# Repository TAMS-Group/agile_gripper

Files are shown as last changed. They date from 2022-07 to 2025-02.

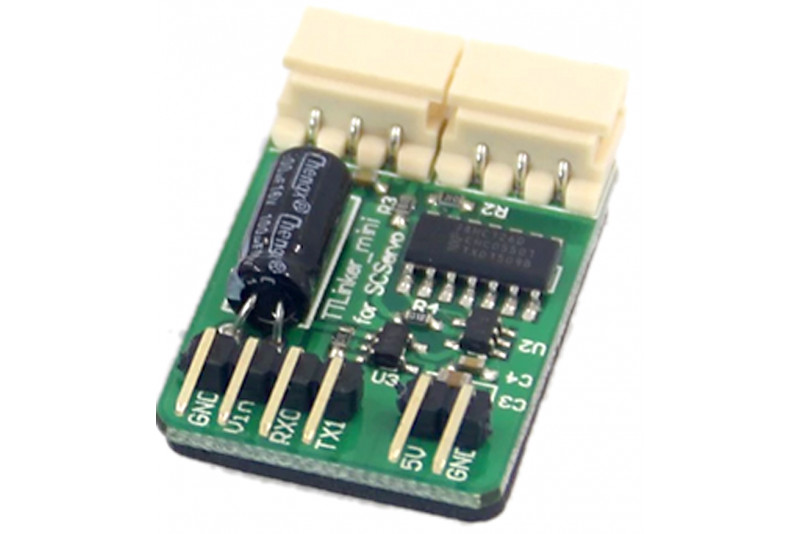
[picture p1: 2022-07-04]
doc/ttlinker-mini-pinout.jpg

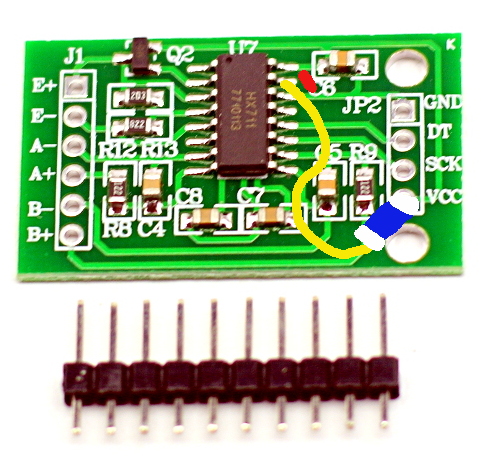
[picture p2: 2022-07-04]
doc/HX711_board_cut_instruction.jpg

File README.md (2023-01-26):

# diana_gripper: Versatile 2-finger 4-servo gripper driven by Feetech SCS digital bus servos

This ROS package provides robot-models and software for a versatile
two-finger gripper using four digital-bus servos from Feetech Inc.

* Using four rotational joints, the gripper can execute parallel
  pinch grasps and tip-pinch grasps, but the fingers can also wrap
  around an object (e.g. a bottle) if needed.

* The fingertips can be easily exchanged. We provide URDF models
  for generic fixed fingers, finray-style flexible fingers,
  and adapters for mounting the camera-based high-res tactile
  DIGIT sensors.

* Both fingers are mounted on a pair of standard load-cells,
  providing measurements of grasping force and shearing force.

* Our Arduino firmware also supports multiple optional 
  finger-mounted IMUs, which can be used to measure vibration,
  impact, and fingertip orientation.

* The SCS-20 servo already provides a lot of sensor inputs,
  including joint (finger) position, velocity, motor torque,
  motor voltage and current, and motor temperature.

## Hardware Overview

## Electronics Overview 

The suggested electronics is based on an Arduino Nano 33 IOT
microcontroller, which includes another IMU (STM LSM6DS3).
The first serial interface (pins RX/TX) of the Nano 33 IOT
is connected to a Feetech "TTLinker Mini" board,
which in turn controls the SCS-20 servos.

Both GY-521 boards are connected to the first I2C-bus (pins A4/A5)
and are powered from the 5V/VUSB pin of the Arduino,
which requires to bridge the corresponding jumper on the
underside of the Nano 33 IOT. 
The GY-521 includes its own 5V->3V3 regulator and data 
communication uses 3V3 levels, compatible with the Nano 33 IOT.
Allocated I2C addresses are 0x68 and 0x69 for the GY-521 boards,
and 0x6A for the on-board LSM6DS3.

The load-cells of both fingers are connected to a common
HX-711 chip breakout board each. The HX-711 provides all
required amplification and filtering circuits together with
a 24-bit ADC running at roughly 80 Hz sample rate.
The digital interface only requires two lines (CLK, Data) each,
connected to the Arduino pins (D2,D3), (D4,D5), (D6,D7), and (D8,D9).

Communication with the host is via USB, and the whole electronics
is bus-powered by the USB. 
Of course, the SCS-20 servos require its own power supply (e.g. 7.2V, 8A).
For now, the 3V3 supply from the Arduino is used to power the load-cells,
as the HX-711 is specified for 2.7..5.5V. Using a stabilitzed
5V supply might increase signal-to-noise ratio. but the 5V USB
is too noisy for that, and another power supply would add to the
hardware complexity.

## udev device detection

The arduino transmits a (unique?) id that can be matched in
udev to identify the serial device. doc/10-diana-gripper-udev.rules
provides a rule file that can be copied to /etc/udev/rules.d/ to add a symlink
/dev/diana_gripper pointing to the correct device.

## Arduino Nano 33 IOT I2C Problems

Maybe try an active bus transceiver or at least a bus terminator, e.g.
https://learn.adafruit.com/adafruit-ltc4311-i2c-extender-active-terminator

See ~/.arduino15/packages/arduino/hardware/samd/1.8.11/cores/arduino/wiring_private.c
and below for the pin assignments and pin capabilities of your specific board.
Then try to edit the source for the Wire library a bit:
/homeL/hendrich/.arduino15/packages/arduino/hardware/samd/1.8.11/libraries/Wire

```
...
void TwoWire::begin(void) {
  //Master Mode
  sercom->initMasterWIRE(TWI_CLOCK);
  sercom->enableWIRE();

  pinPeripheral(_uc_pinSDA, g_APinDescription[_uc_pinSDA].ulPinType);
  pinPeripheral(_uc_pinSCL, g_APinDescription[_uc_pinSCL].ulPinType);
  // FNH! I2C always dying on Arduino Nano 33 IOT... see cores/arduino/wiring_private.c
   PORT->Group[g_APinDescription[_uc_pinSDA].ulPort].PINCFG[g_APinDescription[_uc_pinSDA].ulPin].reg |= (uint8_t) (PORT_PINCFG_DRVSTR);
   PORT->Group[g_APinDescription[_uc_pinSCL].ulPort].PINCFG[g_APinDescription[_uc_pinSCL].ulPin].reg |= (uint8_t) (PORT_PINCFG_DRVSTR);
   // FNH end 
}
...
```

## Servo-Commander firmware

The SCS commander utility scans the bus for devices and reports
all detected servos, together with their protocol type.
Once the initial scan is completed, the commander enters an
interactive loop where the user can select the active servo
and then execute read/write commands on the selected servo.

The SCS commander is not using ROS. 
The program is supposed to be used with a terminal application
or the serial console from the Arduino IDE.
All commands should be terminated by a \n character, either
\f (linefeed) or \r (carriage-return) or both.

* S <id>\n : select servo at address <id> (decimal 3..253) for 
  the next commands.

* i\n :    print motor current (SCS) (may read -1: not implemented by servo)
* j\n :    print motor current (SMS) as multiple of 0.01A 

* l\n :    print motor load (torque) (SCS), unknown units
* m\n :    print motor load (torque) (SMS), unknown units

* p\n :    print motor position (SCS), counts (0..1023)
* q\n :    print motor position (SMS), counts (0..4095)

* t\n :    print servo temperature  (degrees celsius)

* v\n :    print servo supply voltage (deci-volts)

* P <pos>\n:  (SCS-only) move to given position (counts) using current
           speed and/or duration

* Q <pos>\n:  (SMS-only) move to given position (counts) using
              current max-speed and max-acceleration

* S <speed>\n: set motion speed for next P/Q command

## Gripper / Hand firmware and command set

The hand microcontroller currently uses ASCII-based communication
with the host, so that debug messages appear as plain text in the
output stream, and motor values are also human-readable. 

The following lists summarize the most common output messages
and commands (input messages), but may be out-of-sync with the
current release. Please check the source code for the actually
implemented versions and their formatting.

### Firmware output ROS topics:

<node_name>/joint_states          (sensor_msgs/JointState)
<node_name>/joint_errors          (sensor_msgs/JointState: pos=pos vel=vel eff=pos-error)
<node_name>/voltages              (sensor_msgs/Joy: axes:raw values)
<node_name>/temperatures          (sensor_msgs/Joy: axes:raw values)
<node_name>/currents
<node_name>/forces_raw            (sensor_msgs/Joy: axes: raw values)
<node_name>/palm_imu_raw          (sensor_msgs/Imu)
<node_name>/left_finger_imu_raw   (sensor_msgs/Imu)
<node_name>/right_finger_imu_raw  (sensor_msgs/Imu)

### Firmware output messages from the hand

* E: servo position errors (current - goal)
 
  E seq_number stamp pos err1 err2 err3 err4

  published as joint_state message on topic ~joint_position_errors
  with <effort> = errors, <pos> = current servo positions, <vel> =
  current servo velocities

* F: "forces" current force measurementss in Ascii format

  F seq_number stamp forces lc1 lc2 lc3 lc4

  Latest raw values from the load-cells, as measured by
  the HX-711 A/D converters.
  No scaling or temperature compensation is
  applied to the values, which are published as joy messages
  on topic ~/forces_raw and zero-biased on ~/forces_cooked.

  Exponential filtering with alpha=0.1 and 0.01 is also 
  applied to the values to generate high-pass filtered versions
  on topics ~force_filtered_10 and  ~forces_filtered_100

* I: "current" servo motor currents (in Feetech units)

  I seq_number stamp amps i1 i2 i3 i4

  published as joy messages on topic ~currents

* M: "moments" servo motor torques (in Feetech units)

  M seq_number stamp trq m1 m2 m3 m4

  Stored in internal variable and sent as part of 
  next '''joint_state message'''. Also re-published as raw-values 
  (servo counts) to the '''~torques''' topic.

* P: "positions" servo positions (in Feetech counts)

  P seq_number stamp pos p1 p2 p3 p4

  Published as joint_state on topic ~joint_states, where
  <position> = incoming positions converted to radians,
  <velocity> = joint velocity in radians/sec calculated from current
               and previous position message (numerical difference),
               or zero unless at least two messages have been received,
  <effort>   = torques from pervious "M" message

* T: "temperatures" current servo temperaturs in degrees celsius

  T seq_number stamp temp t1 t2 t3 t4 t5 t6 t7

  published as joy messages on topic ~temperatures

* U: "voltages" current servo supply voltages (in deci-volts)

  U seq_number stamp volts u1 u2 u3 u4 u5 u6 u7

  published as joy messages on topic ~voltages

* V: "velocities" current servo velocities (in Feetech units)

  V seq_number stamp vel v1 v2 v3 v4 v5 v6 v7

  currently not used or re-published as ROS message

### Text-commands currently supported by the hand firmware:

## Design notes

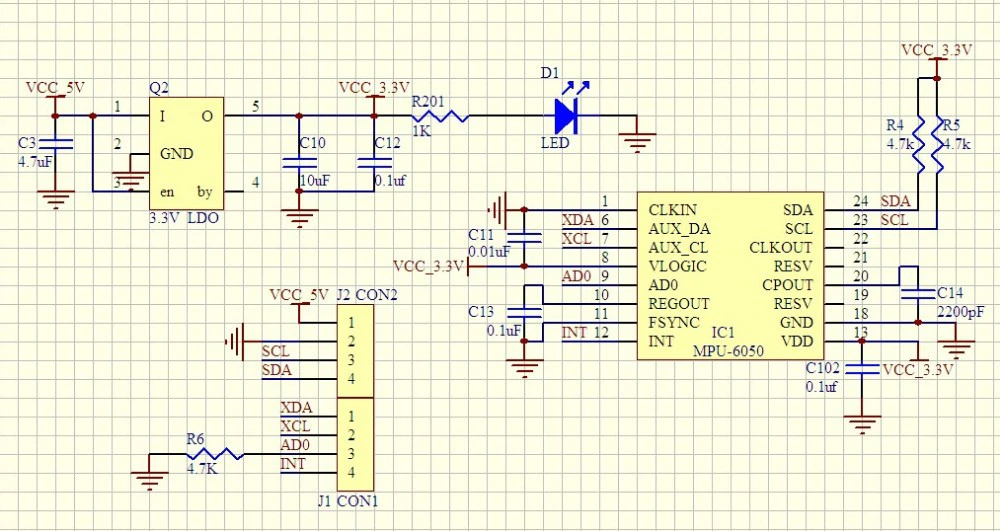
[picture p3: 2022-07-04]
doc/GY-521-schematics.png

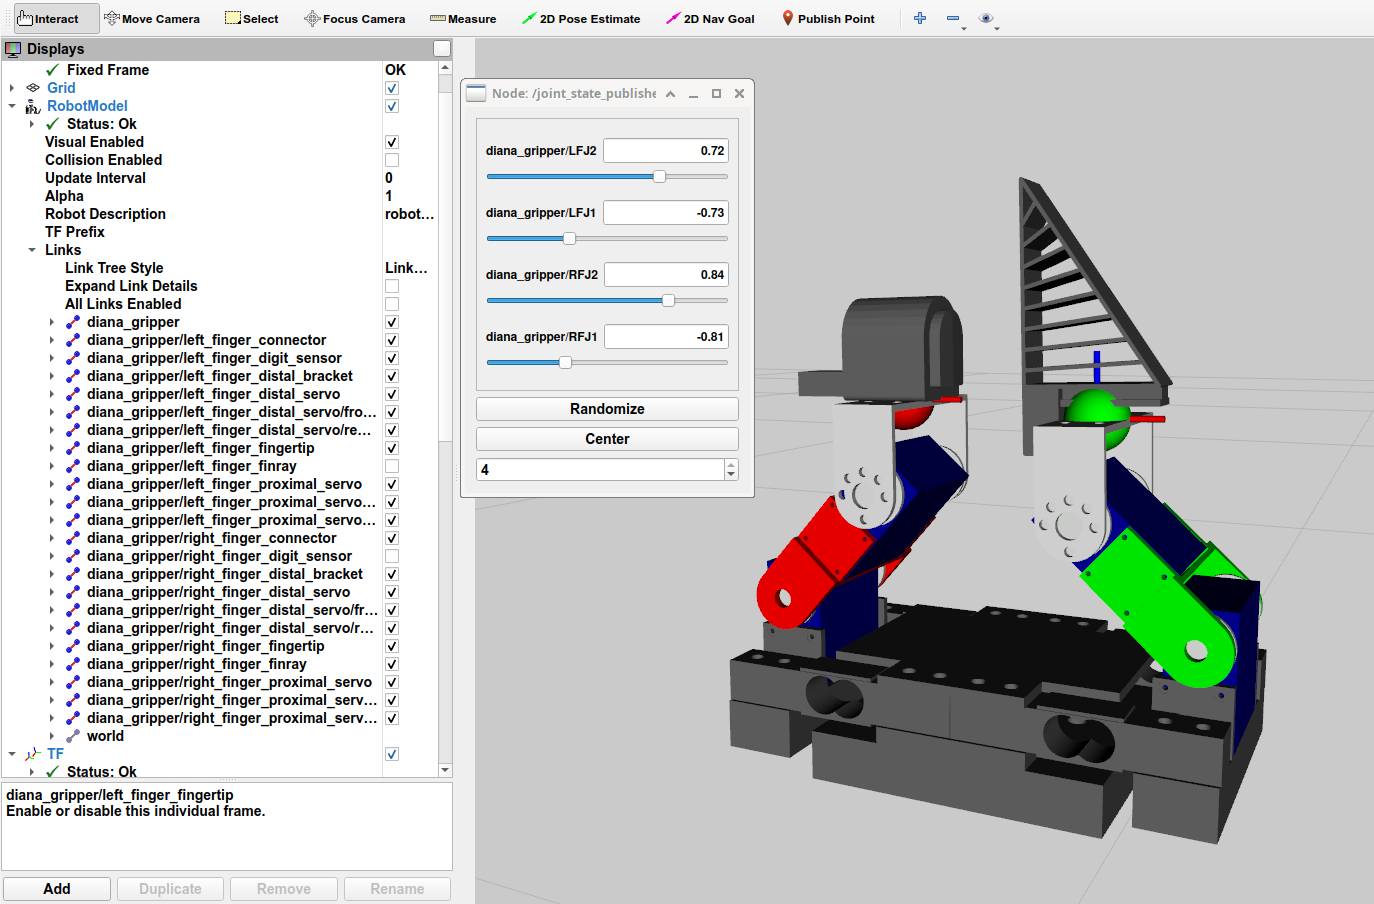
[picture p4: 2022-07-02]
doc/diana_gripper_digit_finray_rviz.png

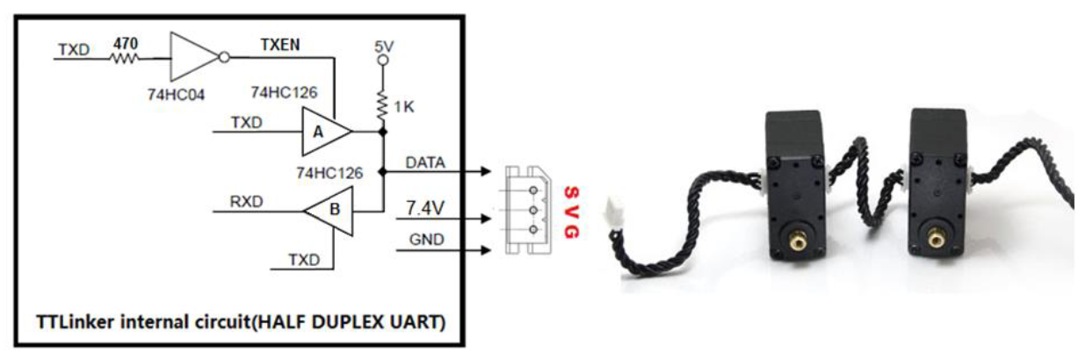
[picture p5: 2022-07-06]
doc/ttlinker-internal-circuit.png

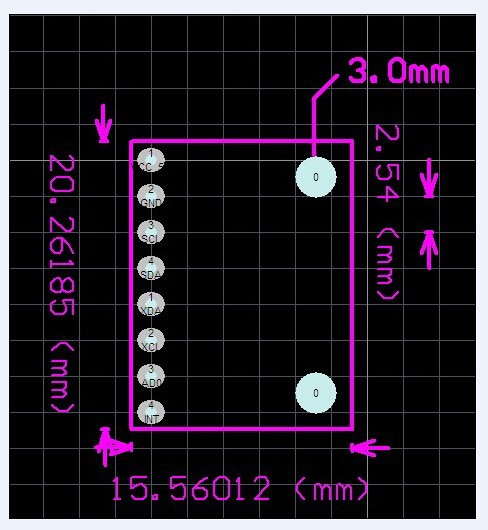
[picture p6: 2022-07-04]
doc/GY-521-dimensions.png

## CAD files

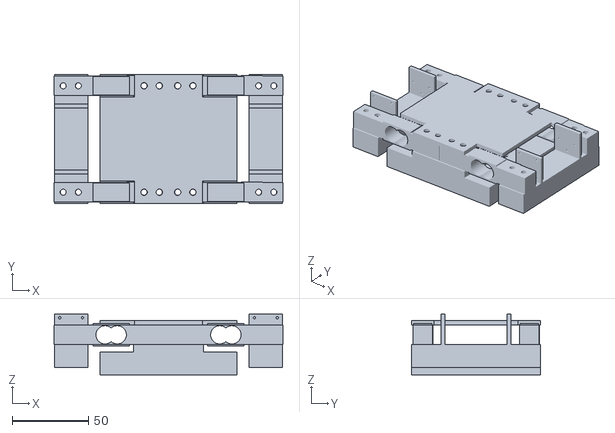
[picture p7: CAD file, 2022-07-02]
meshes/diana_gripper_base_complete_v1.stl
150.6 x 85.0 x 40.0

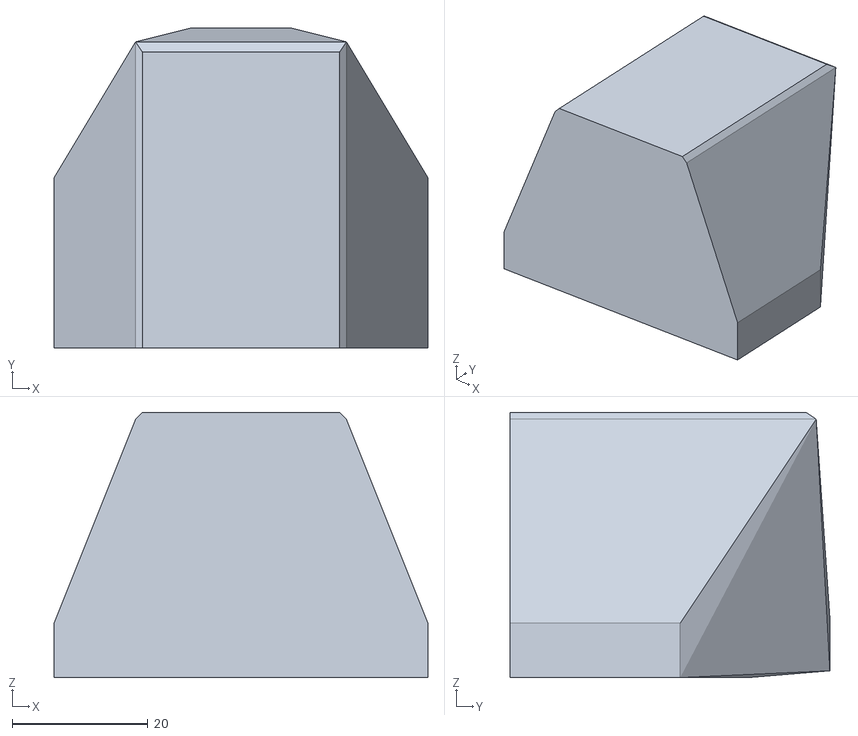
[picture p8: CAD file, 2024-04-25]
meshes/multitip_hull.stl
55.0 x 47.0 x 39.0

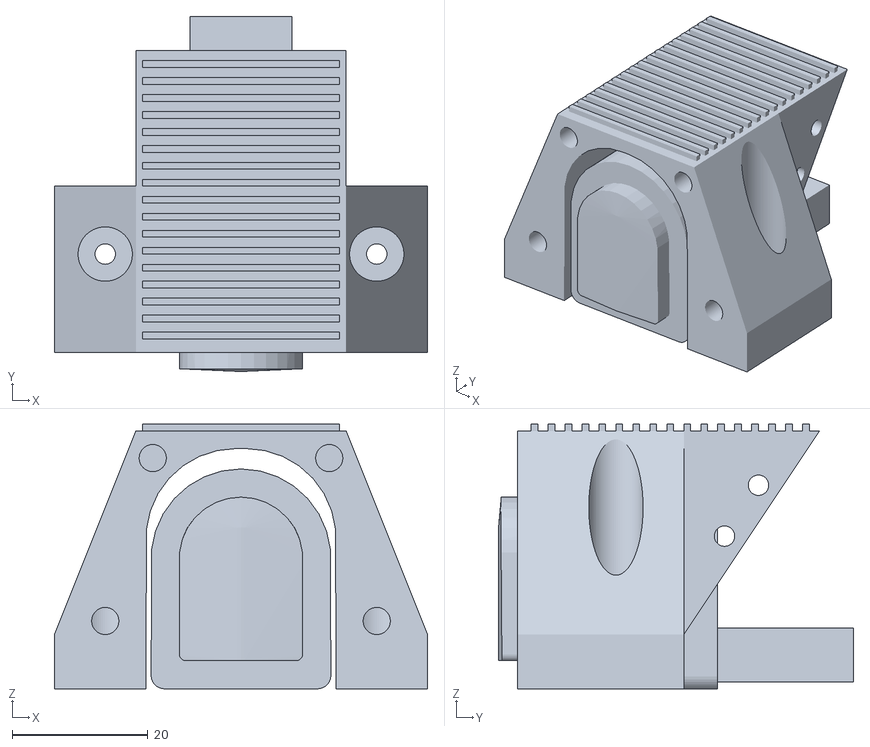
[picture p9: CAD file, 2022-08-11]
meshes/multitip.stl
55.0 x 52.3 x 39.0

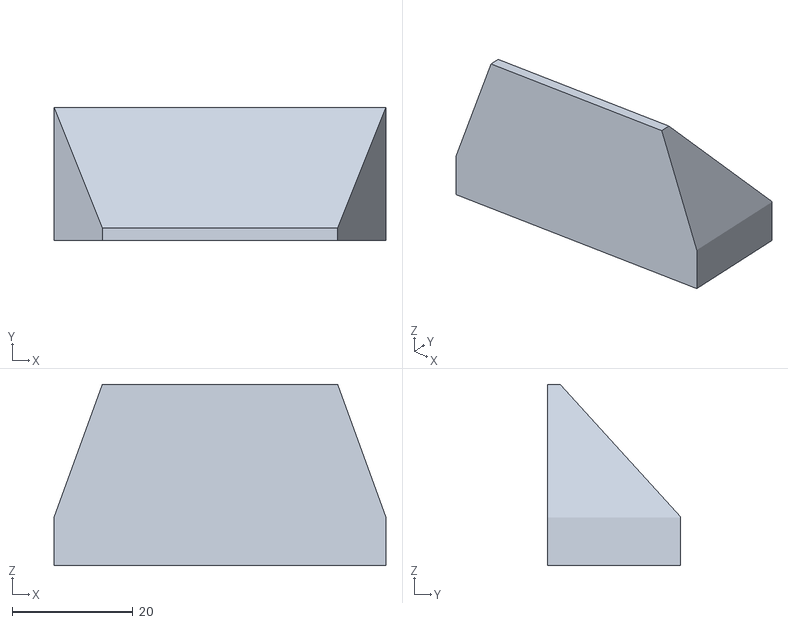
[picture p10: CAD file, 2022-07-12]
meshes/fingertip_simple_hull.stl
55.0 x 22.0 x 30.0

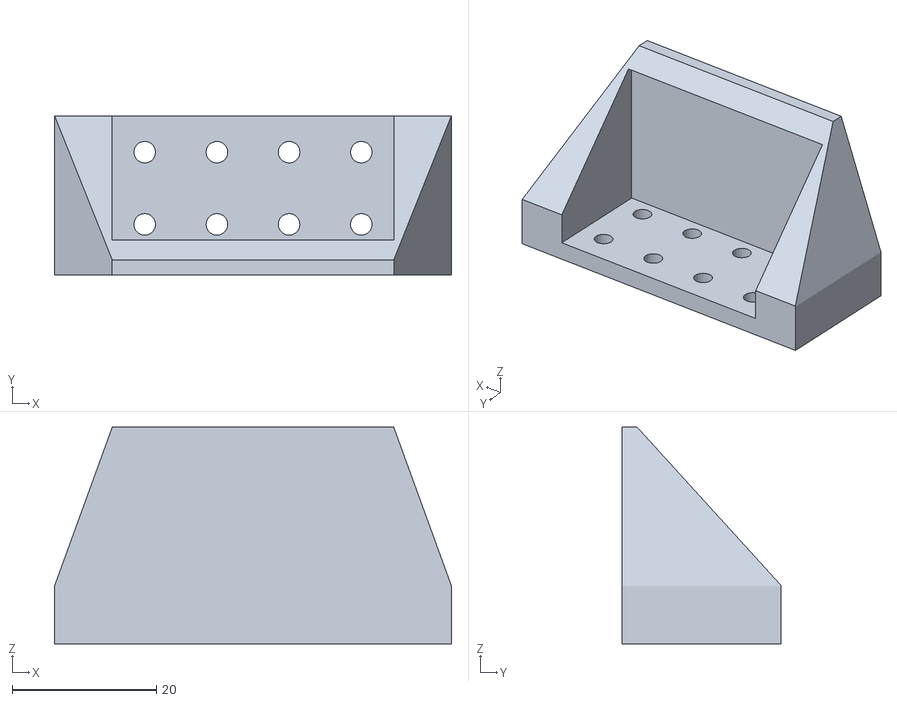
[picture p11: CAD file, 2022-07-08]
meshes/fingertip_simple.stl
55.0 x 22.0 x 30.0

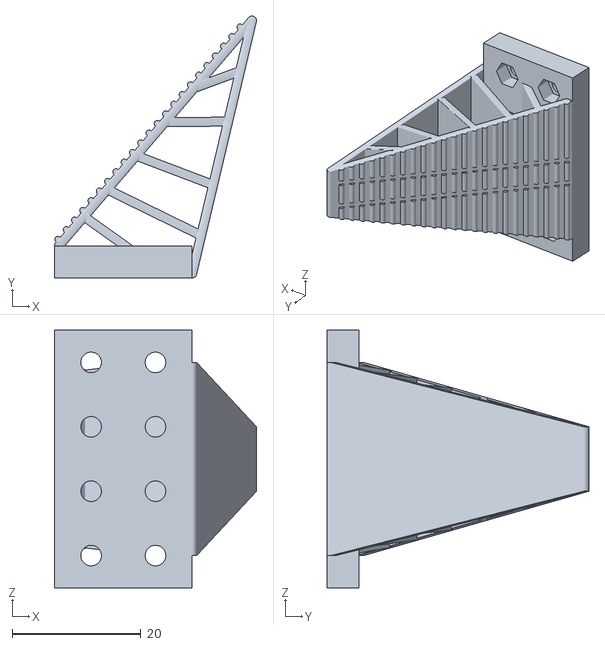
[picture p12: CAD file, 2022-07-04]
meshes/finray_finger_slanted_ridges.stl
31.4 x 40.7 x 40.0

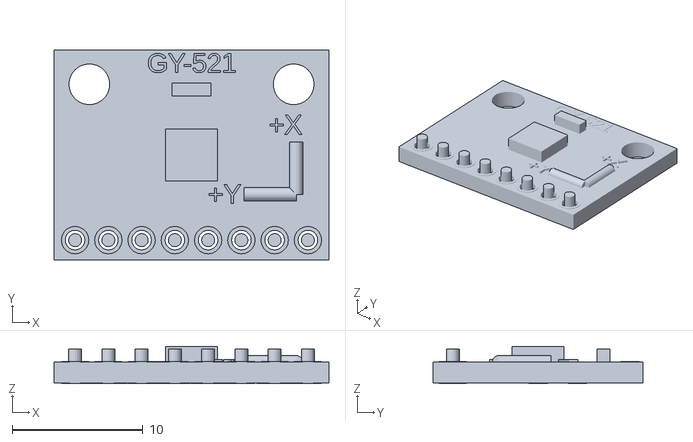
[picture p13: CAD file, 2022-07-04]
meshes/imu_gy521.stl
21.0 x 16.0 x 2.85

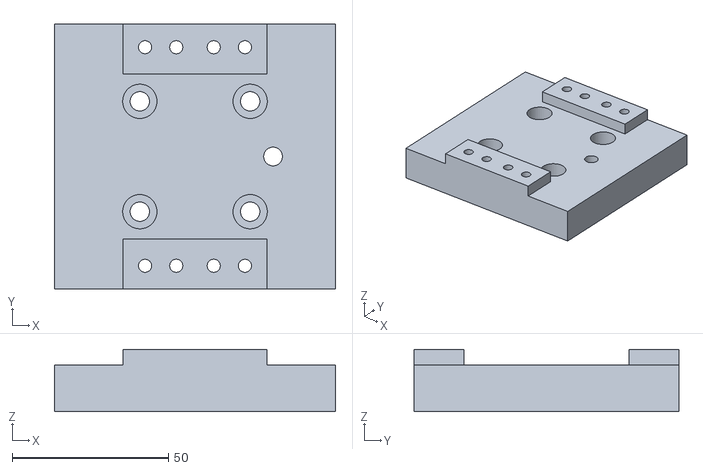
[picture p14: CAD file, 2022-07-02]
meshes/diana_gripper_base_v1.stl
90.0 x 85.0 x 20.0

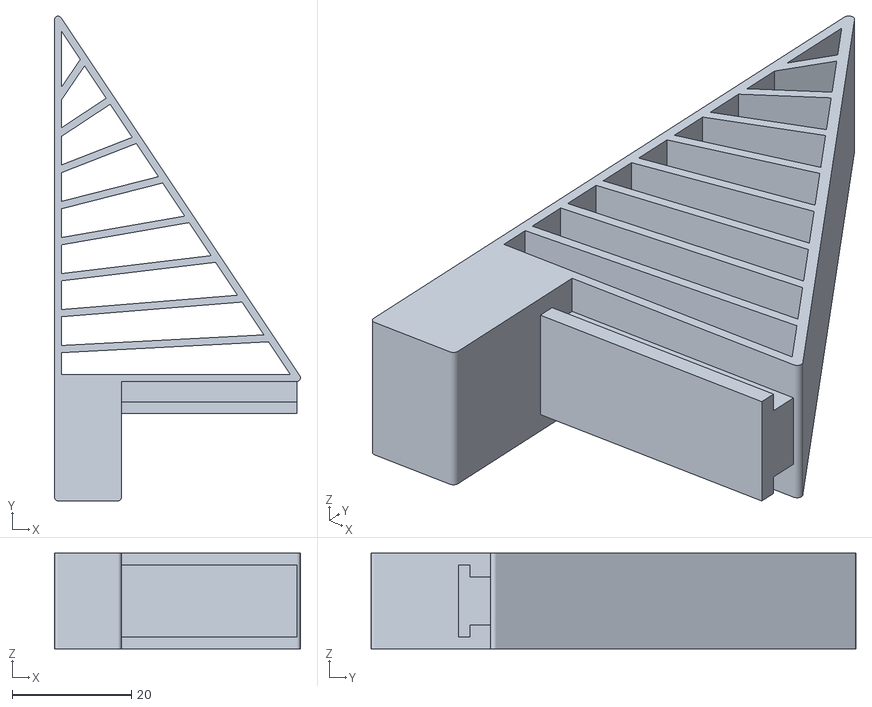
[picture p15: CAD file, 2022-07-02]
meshes/finray_finger.stl
41.2 x 81.2 x 16.0

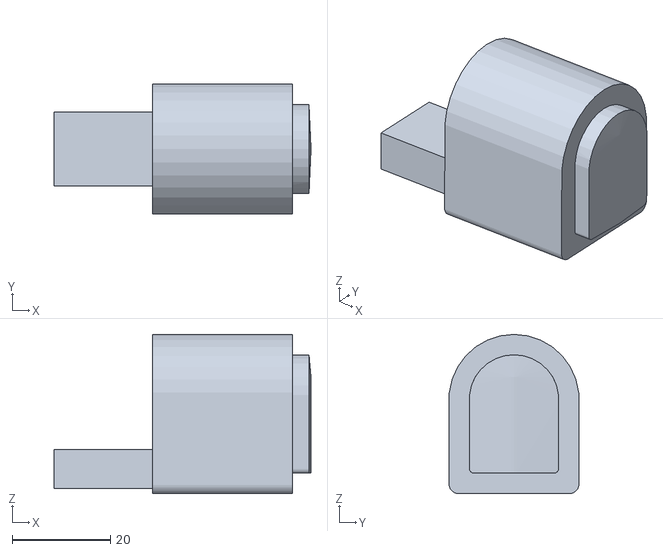
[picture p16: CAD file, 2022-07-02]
meshes/digit_sensor.stl
52.3 x 26.5 x 32.4

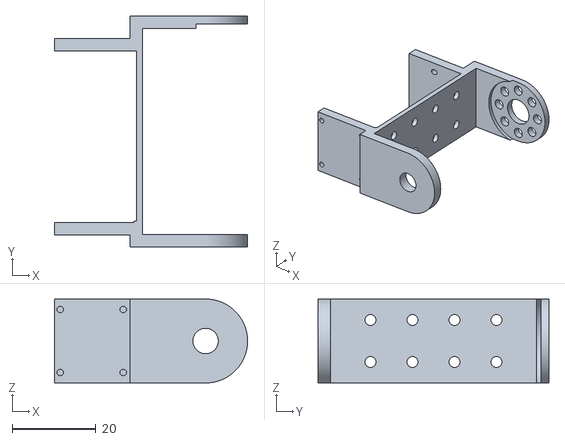
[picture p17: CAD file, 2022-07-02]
meshes/diana_gripper_connector_v1.stl
46.0 x 55.0 x 20.0

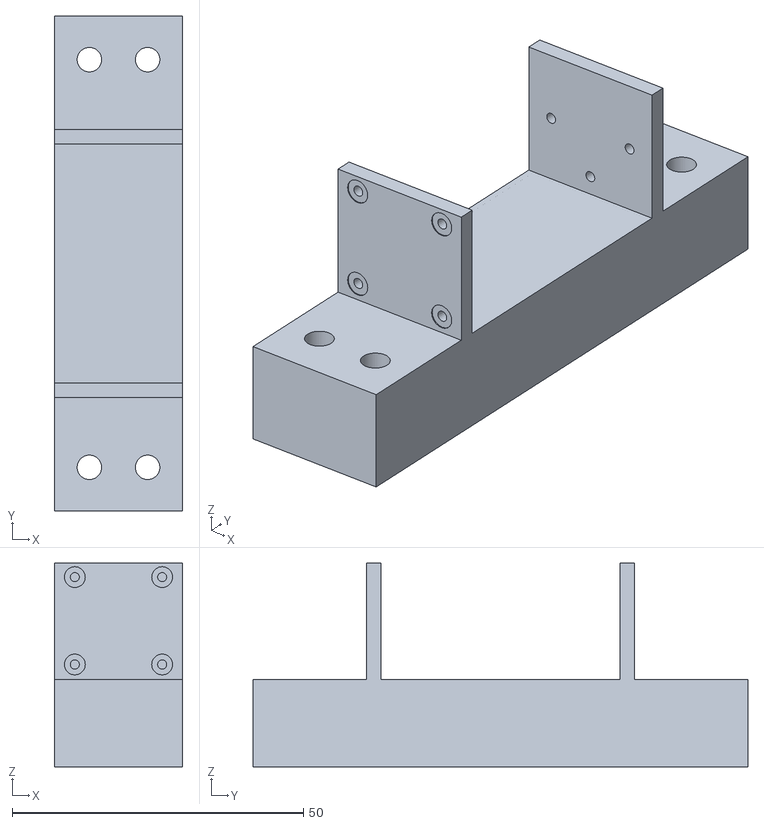
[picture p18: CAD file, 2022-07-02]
meshes/diana_gripper_servo_base_v1.stl
22.0 x 85.0 x 35.0

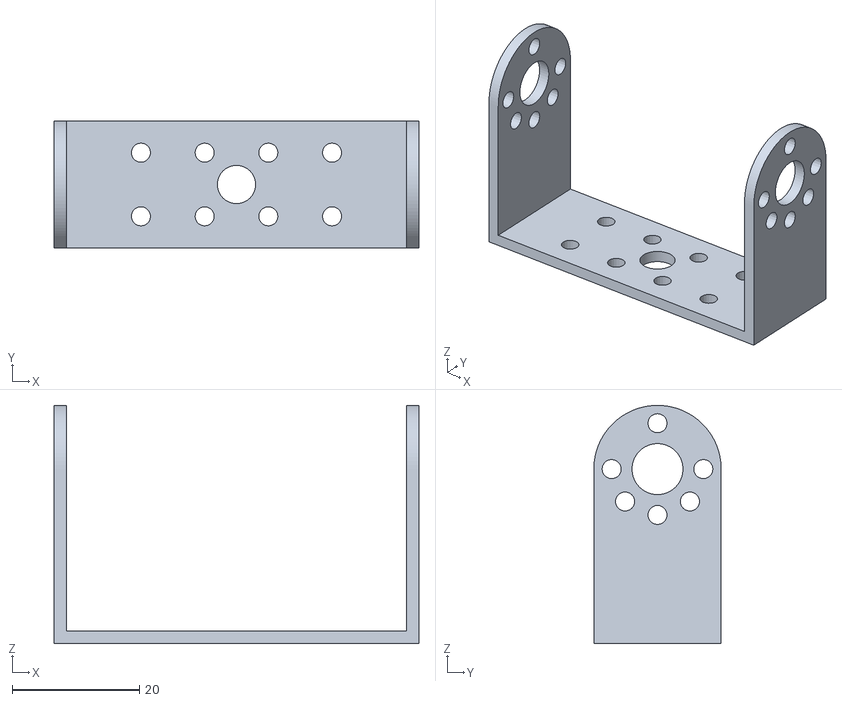
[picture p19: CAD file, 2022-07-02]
meshes/feetech_bracket_big.stl
57.3 x 20.0 x 37.4

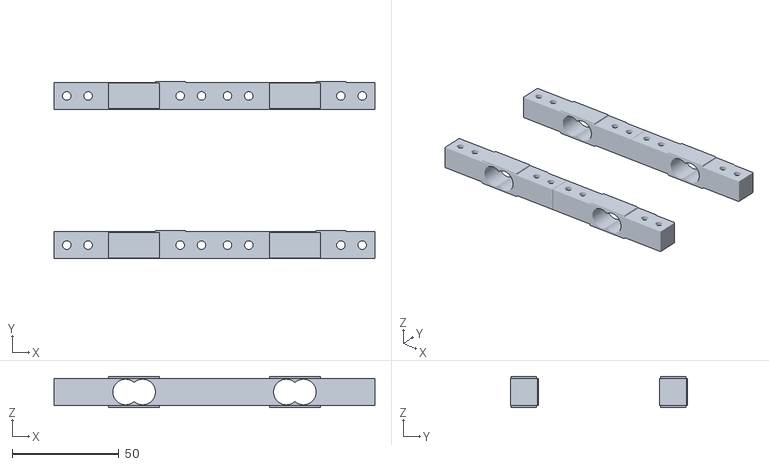
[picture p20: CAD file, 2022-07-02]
meshes/diana_gripper_four_loadcells_v1.stl
150.6 x 83.2 x 14.7

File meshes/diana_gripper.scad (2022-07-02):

/** simple four-servo two-finger gripper with mountplate for
 *  the Agile Robots Diana7 robot.
 *
 * 2022.07.01 - export first meshes (v1)
 * 2022.07.01 - created (based on feetech-servo-hand.scad)
 *
 * (c) 2021, 2022 fnh, hendrich@informatik.uni-hamburg.de
 */


fn = 100;
eps = 0.01;
M6_bore = 6.2;
M4_bore = 4.2;

ddx = 75/2 + 0.2;
ddy = 35;
ddz = 15 + 5 + 12.7/2;

make_diana_flange = 1;
make_gripper_base = 1;
make_palm_plate   = 1;
make_servo_base1  = 1; // first finger
make_connector1   = 1;

make_servo_base2  = 1; // second finger
make_connector2   = 1;

show_loadcells    = 1;

show_servo1P      = 1; // first finger, proximal
show_servo1D      = 1; // first finger, distal
show_bracket1     = 1; // first finger, distal mounting bracket
show_digit1       = 1; // first finger, DIGIT sensor

show_servo2P      = 1; // second finger, proximal
show_servo2D      = 1; // second finger, distal
show_bracket2     = 1; // second finger, distal mounting bracket
show_digit2       = 1; // second finger, DIGIT sensor

if (make_diana_flange) diana_flange();
if (make_gripper_base) gripper_base();
if (make_palm_plate)   translate( [0,0, 15+5+12.7] ) palm_plate();

if (make_servo_base1)  translate( [75.0-6-5,0,20] ) servo_base();
if (make_servo_base2)  translate( [-75.0+6+5,0,20] ) servo_base();
               


if (show_loadcells) {
translate( [ ddx,  ddy, ddz] ) load_cell_komputer_10kg();   
translate( [-ddx,  ddy, ddz] ) load_cell_komputer_10kg();   
translate( [ ddx, -ddy, ddz] ) load_cell_komputer_10kg();   
translate( [-ddx, -ddy, ddz] ) load_cell_komputer_10kg();   
}





if (show_servo1P) {
translate( [75-10,20,50] ) rotate( [0,90,90] ) feetech_scs20_servo( extrude_21mm_axles=0);
translate( [75-10,20+6,50] ) rotate( [0,90,-90] ) feetech_servo_disc( extrude_screws_length=0, extrude_screws_head=[] );
// translate( [75-10,-20-6,50] ) rotate( [0,90,90] ) feetech_servo_disc( extrude_screws_length=0, extrude_screws_head=[] );
}

if (make_connector1) 
translate( [45,1,50] ) rotate( [-90,0,-90] ) // for complete model
// rotate( [-90,0,-90] ) translate( [0,0,-20] ) // for standalone rendering
proximal_medial_connector();

if (show_servo1D) {
translate( [75-10-47,20,50] ) rotate( [-90,0,0] ) feetech_scs20_servo( extrude_21mm_axles=0);
translate( [75-10-47,20+6,50] ) rotate( [0,90,-90] ) feetech_servo_disc( extrude_screws_length=0, extrude_screws_head=[] );
translate( [75-10-47,-20-6,50] ) rotate( [0,90,90] ) feetech_servo_disc( extrude_screws_length=0, extrude_screws_head=[] );
}

if (show_bracket1) 
// translate( [18,0,15+5+30+27.5] ) rotate( [0,180,90] ) 
feetech_scs_bracket_big();

if (show_digit1) 
translate( [ 18,0,90] ) rotate( [0,0,180]) 
digit_sensor();




if (show_servo2P) {
translate( [-(75-10),20,50] ) rotate( [0,90,90] ) feetech_scs20_servo( extrude_21mm_axles=0);
translate( [-(75-10),20+6,50] ) rotate( [0,90,-90] ) feetech_servo_disc( extrude_screws_length=0, extrude_screws_head=[] );
// translate( [-(75-10),-20-6,50] ) rotate( [0,90,90] ) feetech_servo_disc( extrude_screws_length=0, extrude_screws_head=[] );
}

if (make_connector2) 
translate( [-45,1,50] ) rotate( [90,0,-90] ) proximal_medial_connector();

if (show_servo2D) {
translate( [-(75-10-47),20,50] ) rotate( [-90,180,0] ) feetech_scs20_servo( extrude_21mm_axles=0);
translate( [-(75-10-47),20+6,50] ) rotate( [0,90,-90] ) feetech_servo_disc( extrude_screws_length=0, extrude_screws_head=[] );
// translate( [-(75-10-47),-20-6,50] ) rotate( [0,90,90] ) feetech_servo_disc( extrude_screws_length=0, extrude_screws_head=[] );
}

if (show_bracket2) 
translate( [-18,0,15+5+30+27.5] ) rotate( [0,180,90] ) feetech_scs_bracket_big();

if (show_digit2) {
translate( [-18,-20,90] ) digit_sensor();
translate( [-18,+20,90] ) digit_sensor();
}

/**
 * hardcoded size palm plate, mounts on load-cell screws
 */
module palm_plate( 
  alpha = 0.9,
  dx = 45, dy = 85, dz = 3, dx2=90,
  load_cell = [75.0, 12.7, 12.7],
  bore_offsets = [-16, -6, 6, 16], // relative to center of palm
  M4_bore=4.2, M4_head_diameter = 7.0+1.0, M4_head_length=4+1.0, M4_screw_length=30, 
)
{
  difference() {
    union() {
      translate( [0,0,dz/2] ) 
        cube( [dx, dy, dz], center=true );
      translate( [0,0,dz/2] ) 
        cube( [dx2, dy-2*15, dz], center=true );
    }
    
     // loadcell mounting bores
    for( ddy=[-35, +35] ) { // loadcell y positions
      for( ddx=bore_offsets ) { // loadcell M4 bores
        translate( [ddx, ddy, -dz-eps] ) 
          cylinder( d=M4_bore, h=dz+ddz+2*eps, center=false, $fn=50 );
        translate( [ddx, ddy, -dz-eps] ) 
          cylinder( d=M4_head_diameter, h=M4_head_length, center=false, $fn=50 );
      }
    }

  }
}


module servo_base(
  alpha = 0.9,
  dx = 6+10+6, dy = 85, dz = 15, ddy = 35,
  dty = 2.5, // thickness of servo mounting "towers"
  servoy = 41.1, // some SCservos are slightly wider than 40.0
  load_cell = [75.0, 12.7, 12.7],
  bore_offsets = [-5, 5], // relative to center of servo_base block!
  M4_bore=4.2, M4_head_diameter = 7.0+1.0, M4_head_length=4+1.0, M4_screw_length=30, 
)
{
  difference() {
    union() {
      // main mounting block
      color( "gold", alpha )
      translate( [0,0,-dz/2] )
        cube( [dx,dy,dz], center=true );
      
      // servo mounting "towers"
      color( "gold", alpha )
      for( ddty=[-servoy/2-dty/2, servoy/2+dty/2] ) 
        translate( [0, ddty,10] )
          cube( [dx, dty, 20], center=true );      
    }
    
    // loadcell mounting bores
    for( ddy=[-35, +35] ) { // loadcell y positions
      for( ddx=[-5, 5] ) { // loadcell M4 bores
        translate( [ddx, ddy, -dz-eps] ) 
          cylinder( d=M4_bore, h=dz+ddz+2*eps, center=false, $fn=50 );
        translate( [ddx, ddy, -dz-eps] ) 
          cylinder( d=M4_head_diameter, h=M4_head_length, center=false, $fn=50 );
      }
    }
    
    // servo mounting bores
    translate( [0,20,30-eps] ) rotate( [0,90,90] ) feetech_scs20_servo( extrude_mounting_screws=dty, extrude_mounting_screws_heads=4 
    );
  }
}


module gripper_base(
  alpha = 0.9,
  dx = 90, dy = 85, dz = 15,
  M6_bore=6.2, M6_head_diameter = 10.0+1.0, M6_head_length=7+1.0, M6_screw_length=20,
  M4_bore=4.2, M4_head_diameter = 7.0+1.0, M4_head_length=4+1.0, M4_screw_length=30,
)
{
  difference() {
    color( "lightgreen", alpha )
    union() {
      // mounting plate for Diana7 flange
      translate( [0,0,dz/2] )
        cube( [dx,dy,dz], center=true );
      
      // extra blocks to mount loadcells, min z-height 3mm for loadcell clearance
      ddz = 5;
      for( dyy =[dy/2-16/2,-dy/2+16/2] )
        translate( [0, dyy,dz+ddz/2] )
          cube( [23+23, 16, ddz], center=true );
    }
    
    // Diana7 M6 D912 screw bores, max length in flange is 12 
    rr = 25.0; 
    for( phi=[0,90,180,270] ) {
      rotate( [0,0,phi+45] ) translate( [rr,0,-eps] )
        cylinder( d=M6_bore, h=dz+2*eps, center=false, $fn=40 );
      rotate( [0,0,phi+45] ) translate( [rr,0,dz-M6_head_length] )
        cylinder( d=M6_head_diameter, h=M6_head_length+2*eps, center=false, $fn=40 );
    }
    // Diana7 alignment pin bore, max depth in flange in 6
    translate( [rr,0,-eps] )
      cylinder( d=6.0, h=dz+2*eps, center=false, $fn=40 );
    
    // loadcell mount bores
    for( ddy=[-35, +35] ) { // loadcell y positions
      for( ddx=[-16,-6, 6,16] ) { // loadcell M4 bores
        translate( [ddx, ddy, -eps] ) 
          cylinder( d=M4_bore, h=dz+ddz+2*eps, center=false, $fn=50 );
        translate( [ddx, ddy, -eps] ) 
          cylinder( d=M4_head_diameter, h=M4_head_length, center=false, $fn=50 );
      }
    }
    
  } // difference
}


/* basic CAD model of the Agile Robots Diana-7 robot tool flange.
 * Centered in x and y, flange aligned at z=0.
 * Note: 45-deg bevels 0.1mm on outer and inner cylinders NOT modelled yet.
 */ 
module diana_flange() {
  hh = 70; dd= 85;
  h2 = 6; d2 = 63; d3 = 31.5;
  rr = 25;
  
  color( "silver" )
  translate( [0,0,-hh-h2] )
    cylinder( d=dd, h=hh+eps, center=false, $fn=200 );
  
  color( "gray" )
  difference() {
    translate( [0,0,-h2] ) 
      cylinder( d=d2, h=h2, center=false, $fn=200 );
    translate( [0,0,-h2-eps] ) 
      cylinder( d=d3, h=h2+2*eps, center=false, $fn=200 );

    // screw bores M6x12
    for( phi=[0,90,180,270] ) 
      rotate( [0,0,phi+45] ) translate( [rr,0,-12+eps] )
        cylinder( d=M6_bore, h=12.0, center=false, $fn=40 );

    // alignment pin bore 6H7, depth 6mm
    translate( [rr,0,-6-1.5*eps] )
      cylinder( d=M6_bore, h=6.0+3*eps, center=false, $fn=40 );
  }
}



module proximal_medial_connector() {
  dxmin = 49; // original: 51.5; 
  tt=3.0; // plate thickness 

  qz = -32.0;
  
  bx1 = -20.7; 
  bx2 =  23.1;
  by = 0;
  bz = 20-2;
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

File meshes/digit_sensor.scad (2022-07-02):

/** simplified mesh for the Facebook DIGIT tactile sensor.
 * 
 * (c) 2022, fnh, hendrich@informatik.uni-hamburg.de
 */
 
 digit_sensor();
 
 
 /**
  * simplified model of the DIGIT sensor.
  * Sensor points towards +x, origin is at the bottom.
  */
 module digit_sensor( usb_connector=[20,15,8], M2_bore=2.2 ) {
   w = 26.5;
   h = 32.4;  // without top ridge
   hh = 33.7; // with ridge  
   l  = 28.5; // without gel
   ll = 32.3; // with gel
   gw = 18.2; // gel width
   gh = 24.6; // gel height
   ss = 10.0; // distance between screws
   sl = 15.0; // screw center from back face
   rb =  2.0; // bottom bevel radius
   uh =  5.0; 
   uw =  9.9;
   ur =  2.0;
   ul =  4.0;

   rc = w/2;  // radius of main housing
   rd = gw/2; // top radius of gel
   re = 1;    // bottom radius of gel part
   border = (w - gw) / 2;

   color( [0.1,0.1,0.1,1.0] )    
   translate( [-sl,0,0] ) 
   difference() {
     hull() {
       translate( [0,+w/2-rb,rb] ) 
         rotate( [0,90,0] ) 
           cylinder( r=rb, h=l, center=false, $fn=30 );
       translate( [0,-w/2+rb,rb] ) 
         rotate( [0,90,0] ) 
           cylinder( r=rb, h=l, center=false, $fn=30 );
       translate( [0,0,h-rc] ) 
         rotate( [0,90,0] ) 
           cylinder( r=rc, h=l, center=false, $fn=30 );
     }
     
     // mounting screws
     translate( [sl, +ss/2, -0.1] ) cylinder( d=M2_bore, h=4, center=false, $fn=20 );
     translate( [sl, -ss/2, -0.1] ) cylinder( d=M2_bore, h=4, center=false, $fn=20 );
   }
   
   color( "white" )
   translate( [-sl,0,0] ) 
   hull() {
     translate( [l,+gw/2-re,border+re] ) 
       rotate( [0,90,0] ) 
         cylinder( r=re, h=ll-l-0.5, center=false, $fn=30 );
     translate( [l,-gw/2+re,border+re] ) 
       rotate( [0,90,0] ) 
         cylinder( r=re, h=ll-l-0.4, center=false, $fn=30 );
     translate( [l,0,h-border-rd] ) 
       rotate( [0,90,0] ) 
         cylinder( r=rd, h=ll-l-0.4, center=false, $fn=30 );
     translate( [ll-8,0,border] )
       cylinder( r=8, h=gh-5, center=false, $fn=100 );
   }
   
   // usb plug
   color( "blue" )
   hull() {
     translate( [-sl-0.1,-uw/2,uh] ) 
       rotate( [0,90,0] ) 
         cylinder( r=ur, h=ul, center=false, $fn=30 );
     translate( [-sl-0.1,+uw/2,uh] ) 
       rotate( [0,90,0] ) 
         cylinder( r=ur, h=ul, center=false, $fn=30 );
   }
   
   // usb connector (if non-zero)
   if (len(usb_connector) == 3) {
     color( "orange" )
     translate( [-sl-usb_connector[0]/2, 0,uh] ) 
       cube( size=usb_connector, center=true );
   }
}
 

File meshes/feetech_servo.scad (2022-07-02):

/** feetech-servos.scad
 * 
 * geometry models of several FeeTech model servos, including:
 * FS5113R          - analog continuous rotation servo
 * SCS15            - 15kg cm 7.4V digital bus servo
 * SCS20-360T/TTL   - 20kg cm 7.4V digital bus servo
 * SCS09            - digital bus micro servo 5V (6V? 7.4V ??)
 *
 * All dimensions are in millimeters as measured by hand, 
 * as no datasheet was available. Precision should be around 0.1mm, 
 * but some rounded edges and fine details are not modeled.
 *
 * Body origin is at the servo axis, z=0 is aligned with the top
 * surface of the motor housing (axis extends into +z).
 * Horn origin is at the bottom of the horn, axis at x=y=0.
 *
 * To simplify the design of housings, use extrude_cable_connector > 0
 * and extrude_mounting_screws > 0 with d_mounting_screws set accordingly.
 *
 * 2021.11.14 - add TTLinker board
 * 2021.01.29 - SCS20 extrude_mounting_screws_heads
 * 2020.11.30 - fix SCS20 size (higher than SCS15!)
 * 2020.11.29 - updated brackets
 * 2020.11.23 - add SCS09 micro servo
 * 2020.11.21 - created (based on adafruit feedback servo)
 * 2019.02.18 - origninal adafruit feedback servo 
 *
 * (c) 2019, 2020 fnh, hendrich@informatik.uni-hamburg.de
 */

eps = 0.1;
fn  = 100;

feetech_demo = 1;

if (feetech_demo) {


translate( [  0, 0,   0] )  feetech_wing_servo();
translate( [ 80, 0, 0] )      feetech_standard_servo();
translate( [ 80, 0, 1.5+10] ) rotate( [0,180,0] ) feetech_servo_disc();

// translate( [  0, 0, 0] )   feetech_scs20_servo( extrude_mounting_screws=7, extrude_mounting_screws_heads=22 );
translate( [ -80,  80,   0] )  feetech_scs20_servo();
translate( [ -80,  0,   0] )  feetech_scs15_servo( extrude_21mm_axles=50, extrude_cable_connectors=10 );
translate( [-160,  0,   0] )  feetech_scs09_servo();
translate( [   0,  0, -50] )  feetech_servo_double_end_disc();

translate( [ 160, 0, 0] )  feetech_scs_bracket_small();
translate( [ 160, 40, 0] ) feetech_scs_bracket_big();

translate( [ 0,80,0] )     adafruit_feedback_servo();
translate( [ 0,80,1.5] )   adafruit_feedback_servo_horn();
  
translate( [   0,150,0] )  servo_disc_adapter_plate();
translate( [  -20,150,0] ) cylinder( d=2.0, h=25.0, center=false );
translate( [   20,150,0] ) bottom_axle_adapter_plate( inbus_head_cut_depth = 1, servo_disc_cut_depth = 0.5 );
translate( [   40,150,0] ) bottom_axle_adapter_plate( bore=8.0, rim=1.0, make_m3_bores=0 );
translate( [  160, 80,0] ) ttlinker( hull=1, pin_length=5.0 );
}




/**
 * SCS20 digital  bus servo, double axis
 */
module feetech_scs20_servo(
  extrude_mounting_screws=2, 
  extrude_mounting_screws_heads=0, 
  d_mounting_screws=1.58,
  d_mounting_screws_heads=3.6,
  extrude_cable_connector=0,
  extrude_21mm_axles=0,
  body_color = [0.4,0.4,0.6],
) 
{
   // main housing 
   sx = 40.2;  // total width, including label stickers (main body 40.0)
   sy = 20.1;  // including label stickers, main body more like 20.0
   sz = 40.5;  // higher than SCS15 (!)
   
   sx_axis_rim = 12.5;
   sz_axis_rim = 1.4;
   dx_axis_rim = sx - 30.3;
  
   d_axle = 5.95; // 24T 25T ?
   h_axle = 4.3;

   sx_fins = 8.0; // size of the "mounting fins"
   sy_fins = sy;
   sz_fins = 2.5;
   dx_fins = sx_fins/2;
   dz_fins = -8.7; // from top surface of the body
   dx_fin_holes = (sx_fins - 4.65); // fron fin center!
   dy_fin_holes = (14.8 - 4.8)/2; // outer distance minus hole radius
   dd_fin_holes = 4.8;

   // axle
   color( "gold" )
   translate( [dx_axis_rim,0,-sz/2] )
     translate( [-dx_axis_rim ,0,sz/2+sz_axis_rim] ) 
       difference() {
         cylinder( d=d_axle, h=h_axle, $fn=fn, center= false );
         cylinder( d=2.5,    h=h_axle+eps, $fn=fn, center= false );
       }

   if (extrude_mounting_screws == 0) {
     color( "red" ) 
       translate( [dx_axis_rim+4,0,0] ) rotate( [0,0,90] ) 
         electronics_label( "FeeTECH", letter_size=3 );


     color( [0.95, 0.95, 0.95] ) 
       translate( [dx_axis_rim+8,0,0] ) rotate( [0,0,90] ) 
         electronics_label( "SCS-20", letter_size=2.5 );
   }
  
   translate( [dx_axis_rim,0,-sz/2] )
   {
     // main housing 
     difference() {
       color( body_color )
         cube( size=[sx, sy, sz], center=true );
       
       // side cable connector holes
       // color( "orange" ) 
       translate( [-5,-sy/2, -sz/2+7.5] )
         cube( [9.5, 2.0, 5.5], center=true );
       // color( "orange" ) 
       translate( [-5,+sy/2, -sz/2+7.5] )
         cube( [9.5, 2.0, 5.5], center=true );

     if (extrude_mounting_screws == 0) {
       // mounting screw holes (top)
       for( dy=[-8, +8] ) 
          for( dx=[-10+6.8] )
            translate( [dx, dy, sz/2] )
              cylinder( d=1.58, h=4.0, $fn=20, center=true );
       for( dy=[-7, +7] )
         translate( [sz/2-3-7, dy, sz/2] )
           cylinder( d=1.58, h=4.0, $fn=20, center=true );
       translate( [sz/2-3, 0, sz/2] )
         cylinder( d=1.58, h=4.0, $fn=20, center=true );
      
       // mounting screw holes (bottom), y distance 15, x distance 15 + 20
       for( dy=[-7.5,+7.5] ) {
          for( dx=[-17.5, +2.5, +17.5] )
            translate( [dx, dy,-sz/2] )
              cylinder( d=1.58, h=4.0, $fn=20, center=true );
        }
      }
     } // difference
     
     if (extrude_mounting_screws > 0) {
       // mounting screw holes (top)
       for( dy=[-8, +8] ) 
          for( dx=[-10+6.8] )
            translate( [dx, dy, sz/2] )
              cylinder( d=d_mounting_screws, h=extrude_mounting_screws, $fn=20, center=false );
          
       for( dy=[-7, +7] )
         translate( [sz/2-3-7, dy, sz/2-eps] )
           cylinder( d=d_mounting_screws, h=extrude_mounting_screws+1.4*eps, $fn=20, center=false );
       translate( [sz/2-3, 0, sz/2-eps] )
         cylinder( d=d_mounting_screws, h=extrude_mounting_screws+1.4*eps, $fn=20, center=false );
      
       // mounting screw holes (bottom), y distance 15, x distance 15 + 20
       for( dy=[-7.5,+7.5] ) {
          for( dx=[-17.5, +2.5, +17.5] )
            translate( [dx, dy,-sz/2-extrude_mounting_screws-eps] )
              cylinder( d=d_mounting_screws, h=extrude_mounting_screws+2*eps, $fn=20, center=false );
        }
      }
      
      if (extrude_mounting_screws_heads > 0) {
        // mounting screw holes (top)
        
        for( dy=[-8, +8] ) 
          for( dx=[-10+6.8] )
            translate( [dx, dy, sz/2+extrude_mounting_screws] )
              cylinder( d=d_mounting_screws_heads, h=extrude_mounting_screws_heads+eps, $fn=20, center=false );
      
        // three holes on bottom of front (driving) side
        for( dy=[-7, +7] )
          translate( [sz/2-3-7, dy, sz/2+extrude_mounting_screws-2*eps] )
            cylinder( d=d_mounting_screws_heads, h=extrude_mounting_screws_heads+2.5*eps, $fn=20, center=false );

        translate( [sz/2-3, 0, sz/2+extrude_mounting_screws-2*eps] )
          cylinder( d=d_mounting_screws_heads, h=extrude_mounting_screws_heads+2.5*eps, $fn=20, center=false );
      
        // mounting screw holes (bottom), y distance 15, x distance 15 + 20
        for( dy=[-7.5,+7.5] ) {
          for( dx=[-17.5, +2.5, +17.5] )
            translate( [dx, dy,-sz/2-extrude_mounting_screws-extrude_mounting_screws_heads+eps] )
              cylinder( d=d_mounting_screws_heads, h=extrude_mounting_screws_heads, $fn=20, center=false );
        }
     }


      
      if (extrude_21mm_axles > 0) {
        // 21mm wide extrusions on top and bottom side, aka "servo disc cutouts"
        color( [0.9, 0.4, 0.4, 0.3] ) 
          translate( [-dx_axis_rim,0,sz/2-eps] )
            cylinder( d=21.0, h=extrude_21mm_axles, $fn=fn, center=false ); 
        color( [0.9, 0.4, 0.4, 0.3] ) 
          translate( [-dx_axis_rim,0,-sz/2-extrude_21mm_axles+eps] )
            cylinder( d=21.0, h=extrude_21mm_axles, $fn=fn, center=false ); 
      }
      
      if (extrude_cable_connector > 0) {
       // side cable connector holes
       translate( [-5,-sy/2-extrude_cable_connector/2+eps, -sz/2+7.5] )
         color( "orange" ) 
         cube( [9.5, extrude_cable_connector, 5.5], center=true );
       translate( [-5,+sy/2+extrude_cable_connector/2-eps, -sz/2+7.5] )
         color( "orange" ) 
         cube( [9.5, extrude_cable_connector, 5.5], center=true );
      }

     // axis rim (top)
     color( [0.4,0.4,0.6] ) 
     translate( [-dx_axis_rim ,0,sz/2] ) cylinder( d=sx_axis_rim, h=sz_axis_rim, $fn=fn, center= false );
     
     // axis rim (bottom)
     color( [0.4,0.4,0.6] ) 
     translate( [-dx_axis_rim ,0,-sz/2-sz_axis_rim] ) cylinder( d=sx_axis_rim, h=sz_axis_rim, $fn=fn, center= false );
     
     // axis stub (bottom)
     color( [0.4,0.4,0.6] ) 
     translate( [-dx_axis_rim ,0,-sz/2-sz_axis_rim-4.0] ) 
       difference() {
         cylinder( d=6.2, h=4.0, $fn=fn, center=false );
         translate( [0,0,-eps] )
           cylinder( d=2.3, h=4.0, $fn=fn, center=false );
       }
   }
} // feetech_scs20_servo
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

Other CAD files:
meshes/diana_gripper_palm_plate_v1.stl
meshes/feetech_servo_hand.scad
meshes/electronics.scad
meshes/fingertip_simple.scad
meshes/finray_finger.scad
meshes/load_cells.scad
meshes/multitip.scad
meshes/multitip_hull.scad

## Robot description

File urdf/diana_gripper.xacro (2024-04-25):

<?xml version="1.0" ?>
<robot xmlns:xacro="http://www.ros.org/wiki/xacro" name="diana_gripper">

  <xacro:property name="KG_CM" value="1" />   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

  <xacro:include filename="$(find diana_gripper)/urdf/scservo.xacro" />
  <xacro:include filename="$(find diana_gripper)/urdf/diana_gripper_gazebo.xacro" />
  <xacro:include filename="$(find diana_gripper)/urdf/imu_gy521.xacro" />
  <xacro:include filename="$(find diana_gripper)/urdf/fingertip.xacro" />

  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


<xacro:macro name="diana_gripper" params="name" >

  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
  <link name="${name}">
      <inertial>
        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
        <origin xyz="0 0 ${0.010}" />
        <mass value="0.2" />
        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
      </inertial>

      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
  </link>

  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

  <xacro:scservo name="${name}/left_finger_proximal_servo" type="scs20" rgba="0.0 0.0 0.6 1.0" gmaterial="Gazebo/Blue">
  </xacro:scservo>

  <xacro:scservo name="${name}/left_finger_distal_servo" type="scs20" rgba="0.0 0.0 0.6 1.0" gmaterial="Gazebo/Blue">
  </xacro:scservo>

  <xacro:scservo name="${name}/right_finger_proximal_servo" type="scs20" rgba="0.0 0.0 0.6 1.0" gmaterial="Gazebo/Blue">
  </xacro:scservo>

  <xacro:scservo name="${name}/right_finger_distal_servo" type="scs20" rgba="0.0 0.0 0.6 1.0" gmaterial="Gazebo/Blue">
  </xacro:scservo>


  <joint name="${name}/left_finger_proximal_servo_mount_joint" type="fixed" >
    <parent link="${name}" />
    <child link="${name}/left_finger_proximal_servo" />
    <origin xyz="${-0.075+0.01} 0 ${0.015+0.005+0.03}" rpy="0 3.1415 0" />
  </joint>

  <joint name="${name}/LFJ2" type="revolute" >
    <parent link="${name}/left_finger_proximal_servo" />
    <child link="${name}/left_finger_connector" />
    <origin xyz="0 0 0" rpy="0 0 0" />
    <axis xyz="0 1 0" />
    <limit lower="-1.571" upper="+1.571" effort="1" velocity="6.28" />
    <dynamics damping="0.7" friction="0.0" />
    <safety_controller soft_lower_limit="-1.57" soft_upper_limit="1.57" k_position="1000" k_velocity="100"/> 
  </joint>

  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

  <link name="${name}/left_finger_connector" >
    <inertial>
      <origin xyz="0 0 0" rpy="0 0 0"/>
      <mass value="0.011" />
      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
    </inertial>

    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
  </link>

  <joint name="${name}/left_finger_distal_servo_mount_joint" type="fixed" >
    <parent link="${name}/left_finger_connector" />
    <child link="${name}/left_finger_distal_servo" />
    <origin xyz="0 0 ${-0.03-0.017}" rpy="0 0 0" />
  </joint>

  <link name="${name}/left_finger_distal_bracket" >
    <inertial>
      <origin xyz="0 0 0" rpy="0 0 0"/>
      <mass value="0.011" />
      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
    </inertial>
    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
  </link>

  <joint name="${name}/LFJ1" type="revolute" >
    <parent link="${name}/left_finger_distal_servo" />
    <child link="${name}/left_finger_distal_bracket" />
    <origin xyz="0 0 0" rpy="0 0 0" />
    <axis xyz="0 1 0" />
    <limit lower="-2.21" upper="+2.21" effort="1" velocity="6.28" />
    <dynamics damping="0.7" friction="0.0" />
    <safety_controller soft_lower_limit="-2.20" soft_upper_limit="2.20" k_position="1000" k_velocity="100"/>
  </joint>

  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
  
  <link name="${name}/left_finger_tip_mount" />


  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
  <joint name="${name}/left_finger_tip_mount_joint" type="fixed">
    <parent link="${name}/left_finger_distal_bracket" />
    <child link="${name}/left_finger_tip_mount" />
    <origin xyz="0 0 ${-0.0275}" rpy="0 3.1415 0" />
  </joint>

  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

  <joint name="${name}/right_finger_proximal_servo_mount_joint" type="fixed" >
    <parent link="${name}" />
    <child link="${name}/right_finger_proximal_servo" />
    <origin xyz="${+0.075-0.01} 0 ${0.015+0.005+0.03}" rpy="0 3.1415 0" />
  </joint>

  <joint name="${name}/RFJ2" type="revolute" >
    <parent link="${name}/right_finger_proximal_servo" />
    <child link="${name}/right_finger_connector" />
    <origin xyz="0 0 0" rpy="0 0 0" />
    <axis xyz="0 -1 0" />
    <limit lower="-1.571" upper="+1.571" effort="1" velocity="6.28" />
    <dynamics damping="0.7" friction="0.0" />
    <safety_controller soft_lower_limit="-1.57" soft_upper_limit="1.57" k_position="1000" k_velocity="100"/> 
  </joint>

  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

  <link name="${name}/right_finger_connector" >
    <inertial>
      <origin xyz="0 0 0" rpy="0 0 0"/>
      <mass value="0.011" />
      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
    </inertial>
    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
  </link>

  <joint name="${name}/right_finger_distal_servo_mount_joint" type="fixed" >
    <parent link="${name}/right_finger_connector" />
    <child link="${name}/right_finger_distal_servo" />
    <origin xyz="0 0 ${-0.03-0.017}" rpy="0 0 0" />
  </joint>

  <link name="${name}/right_finger_distal_bracket" >
    <inertial>
      <origin xyz="0 0 0" rpy="0 0 0"/>
      <mass value="0.011" />
      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
    </inertial>
    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
  </link>

  <joint name="${name}/RFJ1" type="revolute" >
    <parent link="${name}/right_finger_distal_servo" />
    <child link="${name}/right_finger_distal_bracket" />
    <origin xyz="0 0 0" rpy="0 0 0" />
    <axis xyz="0 -1 0" />
    <limit lower="-2.21" upper="+2.21" effort="1" velocity="6.28" />
    <dynamics damping="0.7" friction="0.0" />
    <safety_controller soft_lower_limit="-2.20" soft_upper_limit="2.20" k_position="1000" k_velocity="100"/>
  </joint>

  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

  <link name="${name}/right_finger_tip_mount" />

  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
  <joint name="${name}/right_finger_tip_mount_joint" type="fixed">
    <parent link="${name}/right_finger_distal_bracket" />
    <child link="${name}/right_finger_tip_mount" />
    <origin xyz="0 0 ${-0.0275}" rpy="0 3.1415 0" />   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
  </joint>

  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

  <xacro:tcp name="${name}"/> 

  <xacro:imu_gy521 parent="${name}/left_finger_tip_mount" name="${name}/left_finger_imu" >
    <origin xyz="0 0.023 0" rpy="0 0 3.141" />
  </xacro:imu_gy521>
  <xacro:imu_gy521 parent="${name}/right_finger_tip_mount" name="${name}/right_finger_imu" >
    <origin xyz="0 0.023 0" rpy="0 0 3.141" />
  </xacro:imu_gy521>

</xacro:macro> 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


<xacro:macro name="dummy_fingertips" >
  <xacro:fingertip name="diana_gripper/left_finger_fingertip" radius="0.005" rgba="1.0 0.0 0.0 1.0" gmaterial="Gazebo/Red" />

  <joint name="diana_gripper/left_finger_fingertip_joint" type="fixed">
    <parent link="diana_gripper/left_finger_tip_mount" />
    <child link="diana_gripper/left_finger_fingertip" />
    <origin xyz="+0.02 0 0.07" rpy="0 0 0" />  
  </joint>

  <xacro:fingertip name="diana_gripper/right_finger_fingertip" radius="0.005" rgba="0.0 1.0 0.0 1.0" gmaterial="Gazebo/Green" />

  <joint name="diana_gripper/right_finger_fingertip_joint" type="fixed">
    <parent link="diana_gripper/right_finger_tip_mount" />
    <child link="diana_gripper/right_finger_fingertip" />
    <origin xyz="-0.02 0 0.07" rpy="0 0 0" />   
  </joint>

</xacro:macro>



<xacro:macro name="tcp" params="name">

  <link name="${name}/tcp" >
  </link>

  <joint name="${name}/tcp_joint" type="fixed" >
    <parent link="${name}" />
    <child link="${name}/tcp" />
    <origin xyz="0 0 0.15" rpy="0 0 0" />
  </joint>
</xacro:macro>

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

</robot>

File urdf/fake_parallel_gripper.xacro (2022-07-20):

<?xml version="1.0" ?>
<robot xmlns:xacro="http://www.ros.org/wiki/xacro" name="fake_parallel_gripper">

  <!-- small standalone "fake" URDF of a 2-joints robot. This can be used
       with joint_state_publisher_gui to operate the diana_gripper as a
       parallel gripper.
  -->

  <link name="fake_parallel_gripper" >
      <inertial/>
      <!-- just a cylinder, in case you want to "visualize" this robot -->
      <visual>
        <origin xyz="0 0 0.1" />
        <material name="fake_parallel_gripper_material">
          <color rgba="0.7 0.7 0.0 1.0" />
        </material> 
        <geometry>
          <cylinder radius="0.2" length="0.2" />
        </geometry>
      </visual>
  </link>

  <link name="fake_parallel_gripper/angle_link" />

  <joint name="parallel_gripper_angle" type="revolute" >
    <parent link="fake_parallel_gripper" />
    <child link="fake_parallel_gripper/angle_link" />
    <origin xyz="0 0 0" rpy="0 0 0" />
    <axis xyz="0 0 1" />
    <limit lower="-1.2" upper="1.2" effort="1" velocity="1" />
  </joint>

  <link name="fake_parallel_gripper/proximal_tilt_link" />

  <joint name="parallel_gripper_proximal_tilt" type="revolute" >
    <parent link="fake_parallel_gripper" />
    <child link="fake_parallel_gripper/proximal_tilt_link" />
    <origin xyz="0 0 0" rpy="0 0 0" />
    <axis xyz="0 0 1" />
    <limit lower="-1.2" upper="1.2" effort="1" velocity="1" />
  </joint>

  <link name="fake_parallel_gripper/distal_tilt_link" />

  <joint name="parallel_gripper_distal_tilt" type="revolute" >
    <parent link="fake_parallel_gripper" />
    <child link="fake_parallel_gripper/distal_tilt_link" />
    <origin xyz="0 0 0" rpy="0 0 0" />
    <axis xyz="0 0 1" />
    <!-- extra large joint limit 2.0 for "combined" DigitSensor gripper, use 1.57 otherwise -->
    <limit lower="-2.0" upper="2.0" effort="1" velocity="1" />
  </joint>



  <link name="world" />

  <joint name="world_fake_parallel_gripper_joint" type="fixed" >
   <parent link="world" />
   <child link="fake_parallel_gripper" />
   <origin xyz="0 0 -1" rpy="0 0 0" />
  </joint>

</robot>

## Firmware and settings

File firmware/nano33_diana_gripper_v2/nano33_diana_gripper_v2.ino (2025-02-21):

/** SCS "diana gripper" driver and demo (nano33_diana_gripper_v1).
 *  
 *  Assumes 115200 baud for the native USB serial interface to the host 
 *  (Serial) and one 1 MBaud port for the SCServo bus at Serial1.
 *  Note that we power the SCservo TTLinker mini driver from 3V3 instead
 *  of the usual 5V, to protect the Arduino from Overvoltage. Otherwise,
 *  add a voltage divider (e.g. 1700Ohm 3300Ohm to the RX pin) and 
 *  solder the USB-V5 pin jumpoer on the Nano 33 IOT.
 * 
 *  Four "HX711" load-cell amplifiers are bit-banged, with  pin 2 (HX711_CLK1) 
 *  and pin 3 (HX711_DATA1) for the first amp, and pins (4,5) (6,7) (8,9)
 *  for the other ADCs.
 *  
 *  Optionally, a Neopixel RGB 12-LED ring can be connected to pin 11, 
 *  controlled via the Adafruit library.
 *  
 *  We also connect two three IMUs, the first one for on the gripper palm 
 *  (STM LSM6DS3, Arduino Nano 33 IOT on-board, address 0x6A). 
 *  Both fingertips mount a GY-521 breakout board with the MPU-6050 chip. 
 *  All IMUs are connected to the first I2C bus using pins A4/A5.
 *  
 *  Note that the GY-521 includes a 3.3V regulator on its VCC pin,
 *  so supply voltage should be 5V, while signal voltage for the
 *  MPU-6050 is 3.3V (but claimed to be 5V tolerant). 
 *  The I2C address is selected by the AD0 pin on the GY-521, low = 0x68 high = 0x69.
 *  The GY-521 comes with either 10K or 2K2 pullups for SDA/SCL; please check
 *  and if necessary replace the pullups with suitable resistors to enable
 *  stable operation.
 *  
 *  GY-521 circuit diagram:
 *  https://playground.arduino.cc/uploads/Main/MPU6050-V1-SCH/index.jpg 
 *  GY-521 hookup guild and tutorial:
 *  https://www.instructables.com/MPU6050-Arduino-6-Axis-Accelerometer-Gyro-GY-521-B/
 *  I2Cdev + MPU6050 libraries:
 *  https://github.com/jrowberg/i2cdevlib/zipball/master
 *  Default I2C address is 0x68 (pull-down), drive AD0 pin high for address 0x69
 *   
 *  Feetech SCS servo addresses assignment: the two finger gripper uses only one
 *  motor, default servo address is <12>.
 * 
 *  The mounted servo is a type SCS-20 and uses the newer SCS protocol
 *  with velocity/acceleration ramps and (coarse) torque and current
 *  readings. The Hall-effect position sensor is continuous with
 *  4096 steps (12-bits) per full rotation.
 *   
 *  SCS-15: idle current 0,     version L=5, H=15    SCS protocol
 *  SCS-20: idle current not 0, version L=9, H=5     SMS protocol
 *  
 *  Approximate acc/vel calibration results:
 *  vel [rad/sec]     = speed [counts] / 666  (* 0.0016)
 *  acc [rad/sec/sec] = accel [counts] * 0.16
 *  
 *  One SCS write transfer takes 6 .. 11 (0xff 0xff ID Fun Dat ... crc) bytes,
 *  or 60..110 usec at 1 MBaud. The read transfers also need to wait for the
 *  servo response. We set a default timeout of 500 usec for all bus transfers;
 *  you may need to increase this when you start using the sync* commands 
 *  that transmit more data.
 *  
 *  TODO:
 *  
 *  History:
 *  
 *  2022.07.09 - several cleanups, add "echo" mode
 *  2022.07.04 - copied from qbsc_gripper
 *  ...
 *  2021.11.26 - created (copy from ugly_hand_v7).
 *  
 *  (c) 2021, 2022 fnh, hendrich@informatik.uni-hamburg.de
 */
 
#include <math.h>
#include <stdlib.h>

#include <algorithm>
#include <vector>
#include <array>

#define  SCS_TIMEOUT_MICROS  500
#include <AsyncDelay.h>




/*
 * serial (bit-banged) interface to HX711 differential strain-gage ADC
 */
#define have_hx711   1
#define N_LOADCELLS  (4)
#include "HX711_LITE.h"

HX711_LITE  loadcells[ N_LOADCELLS ];
long        loadcell_data[ N_LOADCELLS ] = { 0L, 0L, 0L, 0L };
long        loadcell_last_read_millis[ N_LOADCELLS ]  = { 0L, 0L, 0L, 0L };
int         loadcell_enabled[ N_LOADCELLS ]    = { 1, 1, 1, 1 };
int         loadcell_errors[ N_LOADCELLS ]     = { 0, 0, 0, 0 };
int         loadcell_clk_pins[ N_LOADCELLS ]  = { 2, 4, 6, 8 };
int         loadcell_data_pins[ N_LOADCELLS ]  = { 3, 5, 7, 9 };




/*
 * IMUs: one built-in LSM6DS3 IMU on board, two external IMUs
 * on the finger(tips).
 */

#include <Arduino_LSM6DS3.h>   // Note: this stupid library *hardcodes* an object called IMU

bool    have_palm_imu = true; // palm IMU is a LSM6DS3, on-board Nano 33 IOT
int     palm_imu_ax, palm_imu_ay, palm_imu_az;
int     palm_imu_gx, palm_imu_gy, palm_imu_gz;


// two InvenSense 6050 6-axis IMUs at I2C addresses 0x68 and 0x69. 
// 
//#include <I2Cdev.h>
#include <MPU6050.h>
#if I2CDEV_IMPLEMENTATION == I2CDEV_ARDUINO_WIRE
    #include "Wire.h"
#endif

bool    have_lf_imu = false;
MPU6050 lf_imu( 0x68 ); // 0x68 for AD0 low, currenty MF (middle-finger)
int16_t     lf_imu_ax, lf_imu_ay, lf_imu_az;
int16_t     lf_imu_gx, lf_imu_gy, lf_imu_gz;

bool    have_rf_imu = false;
MPU6050 rf_imu( 0x69 ); // 0x69 for AD0 high, currently TH (thumb)
int16_t     rf_imu_ax, rf_imu_ay, rf_imu_az;
int16_t     rf_imu_gx, rf_imu_gy, rf_imu_gz;

// if needed, scale IMU values back from float to (signed int 16),
// current library sets 2000 deg/sec gyro range and 4G acc range, 104 Hz,
// see ~/Arduino/Libaries/Arduino_Arduino_LSM6DS3/src for sources...
// 
#define GYRO_TO_INT   (32768.0 / 2000.0)
#define ACC_TO_INT    (32768.0 / 4.0)


/* 
 * optional Neopixel RGB 12-ring connected to pin 11
 */
#include <Adafruit_NeoPixel.h>

Adafruit_NeoPixel neopixel_ring  = Adafruit_NeoPixel(12, 11, NEO_GRB + NEO_KHZ800);


/*  
 * Feetech SCServo stuff 
  */
#include "SCSCL.h"
#include "SMSCL.h"

SCSCL scs; // older/smaller SC servos
SMSCL sms; // newer/bigger SM servos

#define LED_PIN  (13)

#define SCS_UNKNOWN 0
#define SCS_SERVO 1
#define SMS_SERVO 2
#define SMM_SERVO 3

// the diana_gripper has four SCS-20 servos: LFJ1 LFJ2 RFJ1 RFJ2
// 
#define N_JOINTS  (4)
#define N_SERVOS  (4)

#define DEG2RAD  (PI/180.0)
#define RAD2DEG  (180.0/PI)
#define DEG2COUNTS  (4096.0/360.0)
#define COUNTS2DEG  (360.0/4096.0)



// abbreviations for all servo(s) (joints)
//
#define LFJ1           (0)
#define LFJ2           (1)
#define RFJ1           (2)
#define RFJ2           (3)


// factory calibration values (joint zero degrees -> Hall-effect counts)
// 
#define LFJ1_P00      2048
#define LFJ2_P00      2048
#define RFJ1_P00      2048
#define RFJ2_P00      2048


typedef enum command_mode {
  idle_mode = 0,
  position_mode = 1,
  velocity_mode = 2,
  trajectory_mode = 3,
  effort_mode = 4,
  teach_mode = 5,
} command_mode_t;


command_mode_t  active_mode = idle_mode;


int  demo_enable = 0;
int  echo_mode = 0; 
int  led_val = 0;
int  t_blink = 0;
int  t_last_command = -3000;
int  t_last_TUV = 0;
int  t_last_temperatures = 0;
int  t_last_voltages = 0;
int  t_last_currents = 0;
int  t_last_torques = 0;
int  t_last_forces = 0;

int  t_last_palm_imu  = 0;
int  t_last_lf_imu    = 0;
int  t_last_rf_imu    = 0;

int  sid = 3;


// note: typical servos specified with 60 degrees ~ 0.1 sec, 
// or 600 degrees / second (max).
// For SMS with Hall-effect sensor, 360 deg = 4096 position counts,
// (angular resolution ~ 0.1 degrees), or about 6800 counts/sec.
// 
int wpspeed = 500; // 10..100 = rather slow; 1000 mid, 5000 fast
int wpaccel = 500; // 10 noticeably soft, 100 ok, 1000 fast
int wptime = 1000;

int verbose = 2;
bool enableDebugMsgs = false;


String serialCommandBuffer = "";


int t_now = 0;
int iteration = 0;
int seq_num = 0;

#define N_SERVOS 4

String servo_names[ N_SERVOS ]          = { "LFJ1", "LFJ2",   "RFJ1",  "RFJ2" };
int    servo_ids[ N_SERVOS ]            = {     20,    21,        22,     23  }; 
int    servo_types[N_SERVOS]            = { SMS_SERVO, SMS_SERVO, SMS_SERVO, SMS_SERVO };
int    servo_open_positions[ N_SERVOS ] = {   1024,  1024,      3072,   3072  };
int    servo_zero_positions[ N_SERVOS ] = {   2048,  2048,      2048,   2048  };
int    servo_flex_positions[ N_SERVOS ] = {   3072,  3072,      1024,   1024  };
int    servo_signs[ N_SERVOS ]          = {     +1,    +1,        -1,     -1  }; // +1: increase on close
int    servo_resolution[ N_SERVOS ]     = {   4096,  4096,      4096,   4096  }; // counts per 2pi

int    servo_enabled[ N_SERVOS ]        = {      1,     1,         1,      1  };
int    servo_timeouts[ N_SERVOS ]       = {      0,     0,         0,      0  };
int    servo_torque_limits[ N_SERVOS ]  = {    512,   512,       512,    512  }; // not yet used

       // defaults are medium acceleration and fast speed (range 1..4095 each)
int    servo_accels[ N_SERVOS ]         = {    100,   100,       100,    100  };
int    servo_speeds[ N_SERVOS ]         = {    500,   500,       500,    500  };

int    joint_position_counts[ N_SERVOS ];
int    joint_velocity_counts[ N_SERVOS ];
int    joint_torque_counts[ N_SERVOS ];
int    last_joint_position_update = 0;

int    joint_position_goals[ N_SERVOS ];
int    joint_position_errors[ N_SERVOS ];



double joint_radians[N_SERVOS];             // radians
double joint_velocities[ N_SERVOS ];        // rad/sec
double joint_torques[ N_SERVOS ];           // Nm

bool   joint_position_counts_initialized = false;
bool   joint_position_goals_initialized = false;



AsyncDelay  scsWatchdog;
AsyncDelay  demoDelay; // start(3000, AsyncDelay::MILLIS); isExpired(); repeat() (from expired); restart() from now

char   print_buffer[128];

void usage() 
{
  Serial.println( "h / ?     print this help" );
  Serial.println( "f         print load cell forces" );
  Serial.println( "p         print servo position (SCS)" );
  Serial.println( "q         print servo position (SMS)" );
  Serial.println();
  Serial.println( "t         print servo temperature" );
  Serial.println( "i         print motor current (SCS)" );
  Serial.println( "j         print motor current (SMS)" );
  Serial.println( "r         <id> <addr> read register value" );
  Serial.println( "v         print supply voltage" );
  Serial.println( "w         <id> <addr> <value>  write register value" );
  Serial.println( "$         print temp + voltages + currents" );
  Serial.println( "#         <int>*7 enable/disable servos" );
  Serial.println( "@         0/1 enable echo mode (test without servos)" );
  Serial.println();
  Serial.println( "A         <int>*4 or <int>*1 set servo accel(s) (SMS) [0 .. 4095]" );
  Serial.println( "B         <int>*4 or <int>*1 set servo speed(s) (SMS) [0 .. 4095]" );
  Serial.println( "C         <int> close fingers by given degrees" );
  Serial.println( "D         start/stop/continue demo" );
  Serial.println( "E         <int>*4 effort goal (counts)" );
  Serial.println( "F         freeze (at current position)" );
  Serial.println( "G         <int>*4 position goal (counts)" );
  Serial.println( "H         move to home (all zero)" );
  Serial.println();
  Serial.println( "K         <int>*3 set neopixel K_olor (r g b)" );
  Serial.println( "L         <int>*4 set single neopixel L_ed (index r g b)" );
  Serial.println( "M         set mode: 0=idle 1=pos 2=vel 3=teach" );
  Serial.println( "N         <rrggbb>*12 set N_eopixel pattern: N 0 255 65535 16711680..." );
  Serial.println( "O         <int> open fingers by given degrees" );
  Serial.println( "P         <int> parallel-grasp pos [1500..2500]" );
  
  Serial.println( "Q         <pos> set servo goal position (SMS) [0 .. 4095]" );
  Serial.println( "Q         <pos> <vel> <acc> set servo goal position (SMS) [0 .. 4095]" );
  // Serial.println( "R         set publishing rate (1/sec) [1 .. 100]" );
  Serial.println( "S         select active servo id (3..253)" );
  Serial.println( "T         <int>*7  set torque limit (counts)" );
  // Serial.println( "U         to be determined" );
  Serial.println( "Y         <int> set verbose level" );
  Serial.println( "Z         set zero bias (load cells)" );
  
  Serial.println( "d / ESC   disable demo (+ freeze) " );
}


void demoDebugMsg( String s ) {
  if (enableDebugMsgs) Serial.print( s ); 
}


void demoDebugMsg2( String s, int value ) {
  if (enableDebugMsgs) { Serial.print( s ); Serial.println( value ); }
}


/**
 * called in reaction to a broken/non-communicating servo.
 * Increments the servo_timeouts[] count for the given servo,
 * and disables the servo when a count of 5 is reached.
 */
void handleServoTimeout( int j ) {
  servo_timeouts[j] ++;
  if (verbose > 1) {
    Serial.print( "### servo timeout, index " );
    Serial.print( j ); 
    Serial.print( " servo-ID " );
    Serial.print( servo_ids[j] );
    Serial.print( " n_timeouts i" );
    Serial.println( servo_timeouts[j] );
  }
  
  if (servo_timeouts[j] > 5) {
    servo_enabled[j] = 0;
    Serial.print( "### servo disabled, index " );
    Serial.print( j ); 
    Serial.print( " servo-ID " );
    Serial.print( servo_ids[j] );
    Serial.print( " n_timeouts i" );
    Serial.println( servo_timeouts[j] );
  }
}


/** 
 * convert the current joint_angle from Feetech "counts" to radians.
 */
float get_joint_angle( int id ) {
  int pos = joint_position_counts[id];

  return 1.0 * pos / servo_resolution[id];
}




/**
 * send a new position goal (in Feetech servo counts) for all servos.
 */
void setJointPositionGoal( int goal_positions[N_SERVOS] )
{
  for( int j=0; j < N_SERVOS; j++ ) {
    joint_position_goals[j] = goal_positions[j];

    if (servo_enabled[j] != 1) continue; // skip disabled servos

    if (servo_types[j] == SCS_SERVO) {
      scsWatchdog.start( SCS_TIMEOUT_MICROS, AsyncDelay::MICROS);
      scs.WritePos( servo_ids[j], goal_positions[j], 100, servo_speeds[j] );
      if (scsWatchdog.isExpired()) handleServoTimeout( j );
    }
    else if (servo_types[j] == SMS_SERVO) {
      scsWatchdog.start( SCS_TIMEOUT_MICROS, AsyncDelay::MICROS);
      sms.WritePosEx( servo_ids[j], goal_positions[j], 
                      servo_speeds[j], servo_accels[j] ); // id, position, speed, accel
      if (scsWatchdog.isExpired()) handleServoTimeout( j );
    }
    else {
      Serial.print( "... unknown servo type " );
      Serial.print( servo_types[j] );
      Serial.println( ", ignored." );
    }
  }
  joint_position_goals_initialized = true;

  if (verbose > 3) {
    Serial.print( "... jointPositionGoal[0]: " );
    Serial.println( goal_positions[0] );
    Serial.flush();              
  }
}


void setServoTorqueLimits( int torque_limits[N_SERVOS] )
{
  if (verbose > 4) Serial.println( "setServoTorqueLimits..." );
  for( int j=0; j < N_SERVOS; j++ ) {
    servo_torque_limits[j] = torque_limits[j];
  }
}



void printStampedIntArray( char* prefix, char* mnemonic, int* data ) 
{
  sprintf( print_buffer, "%s %d %d %s %d %d %d %d\n",
                 prefix, 
                 (seq_num++) & 0xff, 
                 millis() & 0xff, 
                 mnemonic, 
                 data[0], data[1], data[2], data[3] );
  Serial.print( print_buffer );
  Serial.flush();                 
}


void printStampedLongArray( char* prefix, char* mnemonic, long* data ) 
{
  sprintf( print_buffer, "%s %d %d %s %ld %ld %ld %ld \n",
                 prefix, 
                 (seq_num++) & 0xff, 
                 millis() & 0xff, 
                 mnemonic, 
                 data[0], data[1], data[2], data[3] );
  Serial.print( print_buffer );
  Serial.flush();                 
}




/**
 * (re-) initialize the SCS bus and try to autodetect all connected servos.
 */
void initSCS() {
  Serial.print( "... initSCS..." );

  Serial1.begin(1000*1000);
  scs.pSerial = &Serial1;
  sms.pSerial = &Serial1;

  int reply;
  int misses = 0;
  for( int id=2; id <= 25; id++ ) { // 253!
    reply = scs.Ping( id );
    if (reply == id) {
      sprintf( print_buffer, "... Servo found at ID %3d %2x ping %d\n", id, id, reply );
      Serial.print( print_buffer ); Serial.flush();

      dumpServoData( id );
      misses = 0;
    }
    else {
      Serial.print( "." );
      misses ++; 
      if (misses > 32) { Serial.println(); misses = 0; }
    }
  }
}



/**
 * reads the current servo positions (in counts) and prints 
 * them in human-readable format.
 */
void sendServoPositions() {
  if (verbose > 4) Serial.print( "... sendServoPositions...\n" );

  int t0 = micros();

  if (echo_mode) {
    printStampedIntArray( "P", "pos", joint_position_goals );
    delay( 8 );
    return;
  }

  for( int j=0; j < N_SERVOS; j++ ) {
    int id   = servo_ids[ j ];
    int type = servo_types[ j ];
    
    // if (verbose > 6) Serial.printf( "... j id type   %d  %d  %d\n", j, id, type );

    if (servo_enabled[j] != 1) {
       // skip, keep latest position estimate intact
       continue;
    }

    if (type == SCS_SERVO) {
      scsWatchdog.start( SCS_TIMEOUT_MICROS, AsyncDelay::MICROS);
      joint_position_counts[j] = scs.ReadPos( id );
      if (scsWatchdog.isExpired()) handleServoTimeout( j );

    }
    else if (type == SMS_SERVO) {
      scsWatchdog.start( SCS_TIMEOUT_MICROS, AsyncDelay::MICROS);
      joint_position_counts[j] = sms.ReadPos( id );
      if (scsWatchdog.isExpired()) handleServoTimeout( j );
    }
    else {
      Serial.print( "... unknown servo type " );
      Serial.println( type );
      Serial.flush();              
    }
  }
  int t2 = micros();

  // Serial.printf( "P %d %d pos %d \n",
  printStampedIntArray( "P", "pos", joint_position_counts );

  joint_position_counts_initialized = true;
  
  if (verbose > 4) {
    sprintf( print_buffer, "... took %d us.\n", (t2-t0) );
    Serial.print( print_buffer );
    Serial.flush();
  }

}


void sendServoVelocities() {
  if (verbose > 4) Serial.print( "... sendServoVelocities...\n" );

  int t0 = micros();

  for( int j=0; j < N_SERVOS; j++ ) {
    int id   = servo_ids[ j ];
    int type = servo_types[ j ];
    
    if (verbose > 6) {
      sprintf( print_buffer, "... j id type   %d  %d  %d\n", j, id, type );
      Serial.print( print_buffer ); Serial.flush();
    }

    if (servo_enabled[j] != 1) {
       // skip disabled servo, keep latest velocity_counts
       continue;
    }

    if (type == SCS_SERVO) {
      scsWatchdog.start( SCS_TIMEOUT_MICROS, AsyncDelay::MICROS);
      joint_velocity_counts[j] = scs.ReadSpeed( id );
      if (scsWatchdog.isExpired()) handleServoTimeout( j );
    }
    else if (type == SMS_SERVO) {
      scsWatchdog.start( SCS_TIMEOUT_MICROS, AsyncDelay::MICROS);
      joint_velocity_counts[j] = sms.ReadSpeed( id );
      if (scsWatchdog.isExpired()) handleServoTimeout( j );
    }
    else {
      sprintf( print_buffer, "... Unknown servo type: %d ignored.\n", type );
      Serial.print( print_buffer ); Serial.flush();
    }
    
    joint_radians[j] = (joint_position_counts[j] - servo_zero_positions[j]) 
                       * servo_signs[j] * COUNTS2DEG;
  }
  int t2 = micros();

  // sprintf( print_buffer, "V %d %d vel %d \n",
  printStampedIntArray( "V", "vel", joint_velocity_counts );
  
  if (verbose > 4) {
    sprintf( print_buffer, "... took %d us.\n", (t2-t0) );
    Serial.print( print_buffer ); Serial.flush();
  }
}


void sendServoTorques() {
  if (verbose > 4) Serial.print( "... sendServoTorques...\n" );

  int t0 = micros();

  for( int j=0; j < N_SERVOS; j++ ) {
    int id   = servo_ids[ j ];
    int type = servo_types[ j ];
    if (verbose > 6) {
      sprintf( print_buffer, "... j id type   %d  %d  %d\n", j, id, type );
      Serial.print( print_buffer ); Serial.flush();
    }

    if (servo_enabled[j] != 1) {
       // skip disabled servo, keep latest torque readings
       continue;
    }

    if (type == SCS_SERVO) {
      scsWatchdog.start( SCS_TIMEOUT_MICROS, AsyncDelay::MICROS);
      joint_torque_counts[j]   = scs.ReadLoad( id );
      if (scsWatchdog.isExpired()) handleServoTimeout( j );
    }
    else if (type == SMS_SERVO) {
      scsWatchdog.start( SCS_TIMEOUT_MICROS, AsyncDelay::MICROS);
      joint_torque_counts[j]   = sms.ReadLoad( id );
      if (scsWatchdog.isExpired()) handleServoTimeout( j );
   }
    else {
      sprintf( print_buffer, "... Unknown servo type: %d ignored.\n", type );
      Serial.print( print_buffer ); Serial.flush();
    }
  }

  int t2 = micros();

  // sprintf( print_buffer, "M %d %d trq %d \n",
  printStampedIntArray( "M", "trq", joint_torque_counts );
  
  if (verbose > 4) {
    sprintf( print_buffer, "... took %d us.\n", (t2-t0) );
    Serial.print( print_buffer ); Serial.flush();
  }
}
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
void loop() {
  iteration ++;
  if ( (iteration < 5) || (iteration == 99) || ((iteration & 0x07ff) == 0x07ff)) {
    sprintf( print_buffer, "... iteration %d\n", iteration ); Serial.flush();
    Serial.print( print_buffer ); Serial.flush();
  }
  
  long t_now = millis();
  
  if ((t_now - t_blink) > 1000) {
    led_val = led_val ^ 1;
    digitalWrite( LED_PIN, led_val );  
    t_blink = t_now;
  }

  // these functions run every loop cycle
  sendServoPositions();
  sendServoTorques();
  sendServoPositionErrors();
  // sendJointVelocities(); // host calculates from pos-diffs

  // every loop cycle, sensor sampling may be auto-throttled
  sendStrainGageForces();

  // every loop cycle, sensor sampling may be auto-throttled
  sendAccelGyro();

  // these functions auto-throttle themselves
  sendServoTemperatures();
  sendServoVoltages();
  sendServoCurrents();


  // check for incoming user/host commands
  if (Serial.available()) {
    handle_command();
  }

  // want to run at ~100 Hz
  long t_now2      = millis();
  long loopMillis  = t_now2 - t_now;
  long sleepMillis = max( 0, 10 - loopMillis );
  if ((verbose > 4) && (loopMillis < 10)) {
    sprintf( print_buffer, "*** loop took %d msec, need extra sleep %d msec...\n", 
                   loopMillis, sleepMillis );
    Serial.print( print_buffer ); Serial.flush();
  }
  delay( sleepMillis );
  // delay( 500 ); // 100 
}

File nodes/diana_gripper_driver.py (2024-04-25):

#! /usr/bin/env python 
#
# diana_gripper_driver.py
#
# Basic Python ROS node to control the 2-fingered "diana_gripper"
# built from four Feetech SCS series servos.
#
# Receives joint_states and other 
# data from the servos and forwards user-commands to the servos.
# Also publishes a sensor_msgs/Joy message with raw sensor data,
# including temperature/voltage/current for the servos.
#
# Provides (text/telnet) style commands on service ~command,
# and accepts joint position/effort goals on topic ~joint_goal.
# In addition, basic parallel-gripper operation is triggered
# by sending a float (radians) to ~simple_goal.
#
# 2022.07.04 - copy from "qbsc_gripper.py" 
# 2021.01.17 - created (based on screwdriver.py)
#
# (c) 2021, 2022 fnh, hendrich@informatik.uni-hamburg.de
#

import collections
import socket
import serial
import math
import numpy as np
import threading
import traceback

# import gc
# gc.set_debug(gc.DEBUG_STATS)
# print( gc )

import rospy
import std_msgs.msg
import sensor_msgs.msg
import control_msgs.msg 

import diana_gripper.srv
# from diana_gripper.srv import TextCommand


# global stuff
#
verbose      = 1
have_text_command = 0
text_command = "?" # help

DEG2RAD = math.pi / 180.0
RAD2DEG = 180.0 / math.pi

def init_joints(hand_name_='diana_gripper'):
    global hand_name, n_joints, joint_names, joint_index
    global js, js_errors
    # left finger / right finger, J2 = proximal J1 = distal  (same as Shadow hand)
    #
    hand_name = hand_name_
    n_joints = 4
    short_joint_names  = ['LFJ2', 'LFJ1', 'RFJ2', 'RFJ1' ]  
    joint_names  = [hand_name + '/' + s for s in short_joint_names]
    joint_index = {}

    for j in range( len(short_joint_names) ):
        joint_index[ short_joint_names[j]] = j
    for j in range( len(joint_names) ):
        joint_index[ joint_names[j]] = j

    if verbose > 3:
        print( joint_index ) # debugging only


    # JointState and raw sensor Joy messages
    #
    js           = sensor_msgs.msg.JointState()  # position + velocities + torques (radians, rad/s, Nm)
    js.name      = joint_names
    js.position  = np.zeros( n_joints )
    js.velocity  = np.zeros( n_joints )
    js.effort    = np.zeros( n_joints )

    js_errors    = sensor_msgs.msg.JointState()  # current pos + current vel + pos error in one message
    js_errors.name      = joint_names;
    js_errors.position  = np.zeros( n_joints )
    js_errors.velocity  = np.zeros( n_joints )
    js_errors.effort    = np.zeros( n_joints )

init_joints()

torques_joy  = sensor_msgs.msg.Joy()         # raw servo torques (counts)
temp_joy     = sensor_msgs.msg.Joy()         # temperatures
volt_joy     = sensor_msgs.msg.Joy()         # voltages 
curr_joy     = sensor_msgs.msg.Joy()         # currents 
forces_joy   = sensor_msgs.msg.Joy()         # strain-gauge forces (raw)

previous_positions_stamp = None
previous_torques_stamp = None
previous_torques = np.zeros( n_joints )
previous_positions = np.zeros( n_joints )

# loadcell stuff
#
n_load_cells = 4
grams_to_newtons = 0.00981
load_cell_bias = np.zeros( n_load_cells )
load_cell_gains = np.ones( n_load_cells )
forces_averaged = []
for i in range( n_load_cells ):
    forces_averaged.append(collections.deque( maxlen=100 ))




# IMU names and messages
#
# imu_names = ['palm_imu', 'LF_imu', 'RF_imu' ] # palm IMU on Arduino nano 33 IOT, two IMUs on middle finger and thumb
imu_names = ['palm_imu' ] # only the main 'palm' IMU
imu_messages = []
imu_raw_joy_messages = []
imu_calibration = []
imu_averaged = {}

for i in range( len(imu_names) ):
    imu_raw_joy_messages.append( sensor_msgs.msg.Joy() )
    imu_messages.append( sensor_msgs.msg.Imu() )
    imu_calibration.append( {} )

    # default gain is 1.0, default bias is 0 counts. Scale depends on the IMU used
    # and the selected sensitivity and should be set via parameters.
    #
    imu_calibration[i][ 'accel_scale' ] = 4.0 * 9.81 / 32768.0  # 4g max at 16-bit signed, default LSM6DS3
    imu_calibration[i][ 'accel_gain_x' ] = 1.0
    imu_calibration[i][ 'accel_gain_y' ] = 1.0
    imu_calibration[i][ 'accel_gain_z' ] = 1.0
    imu_calibration[i][ 'accel_bias_x' ] = 0.0
    imu_calibration[i][ 'accel_bias_y' ] = 0.0
    imu_calibration[i][ 'accel_bias_z' ] = 0.0

    imu_calibration[i][ 'gyro_scale' ] = 250.0 * DEG2RAD / 32768  # 250 deg/s max at 16 bit signed
    imu_calibration[i][ 'gyro_gain_x' ] = 1.0
    imu_calibration[i][ 'gyro_gain_y' ] = 1.0
    imu_calibration[i][ 'gyro_gain_z' ] = 1.0
    imu_calibration[i][ 'gyro_bias_x' ] = 0.0
    imu_calibration[i][ 'gyro_bias_y' ] = 0.0
    imu_calibration[i][ 'gyro_bias_z' ] = 0.0

    # running averages stuff (note: raw data)
    imu_averaged[ imu_names[i] ] = {}

    for k in ['ax', 'ay', 'az', 'gx', 'gy', 'gz']:
        imu_averaged[ imu_names[i] ][ k ] = collections.deque( maxlen=100 )

# print( '>>>>>>> len(imu) ' + str( len( imu_calibration )))


# default servo calibration (including cw/ccw rotation direction)
# 
LFJ1 = {}
LFJ1[ -90 ] =  2120-1024
LFJ1[   0 ] =  2120
LFJ1[ +90 ] =  2120+1024

LFJ2 = {}
LFJ2[ -90 ] =  2048-1024
LFJ2[   0 ] =  2048
LFJ2[ +90 ] =  2048+1024

RFJ1 = {}
RFJ1[ -90 ] =  2008+1024
RFJ1[   0 ] =  2008
RFJ1[ +90 ] =  2008-1024

RFJ2 = {}
RFJ2[ -90 ] =  2048+1024
RFJ2[   0 ] =  2048
RFJ2[ +90 ] =  2008-1024

joint_offsets = [ 2120, 2048, 2008, 2048 ]
joint_scale   = [ 1024.0/90.0, 1024.0/90.0, 1024.0/90.0, 1024.0/90.0 ] # degrees
vel_scale     = [ 1.0/4096, 1.0/4096, 1.0/4096, 1.0/4096 ]  # SMS servo 4096 steps/2pi SCS 1024 steps/2pi
servo_signs   = [ +1, +1, -1, -1 ]

mutex = threading.Lock()
joint_state_goal= sensor_msgs.msg.JointState()
have_new_motion_goal = False


def getp( j, counts ):  # joint_index and raw position counts 
     value = DEG2RAD*( (counts - joint_offsets[j]) * servo_signs[j] / joint_scale[j])
     return value


def getv( j, counts ):
     value = DEG2RAD * counts * vel_scale[j]
     return value


def radians_to_counts( j, radians ): # map ROS angle (rad) to SCS servo #j counts
     value = int( joint_offsets[j] + (radians * RAD2DEG)*servo_signs[j]*joint_scale[j] )
     # print( "radians_to_counts: joint " + str(j) + " radians " + str(radians) + " -> " + str( value ))
     return value
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

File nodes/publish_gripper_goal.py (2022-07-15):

#! /usr/bin/env python 
# publish_gripper_goal.py - publishes a demo Moveit trajectory goal to the fjtas controller
# 
#

print( "#### 1 ####" )

import rospy
import trajectory_msgs.msg
import control_msgs.msg
import actionlib

print( "#### 2 ####" )

rospy.init_node('diana_gripper_goal_publisher', anonymous=False, disable_signals=True )

pub = rospy.Publisher( '/diana_gripper_controller/follow_joint_trajectory/goal',
                       control_msgs.msg.FollowJointTrajectoryActionGoal,
                       queue_size=1 )

print( "#### 3 ####" )

msg = control_msgs.msg.FollowJointTrajectoryActionGoal()
msg.header.seq = 2
msg.header.stamp = rospy.Time.now()
msg.header.frame_id = "HUGO"

msg.goal_id.stamp = msg.header.stamp
#msg.goal_id.id = "/move_group-5-1657298927.312892807"
msg.goal_id.id = "/move_group-5-" + str( rospy.Time.now() )

print( "#### 4 ####" )

msg.goal.trajectory.header.stamp = rospy.Time( 0 )
msg.goal.trajectory.joint_names = ["diana_gripper/LFJ1", "diana_gripper/LFJ2", "diana_gripper/RFJ1", "diana_gripper/RFJ2"]
msg.goal.trajectory.points = []
p1 = trajectory_msgs.msg.JointTrajectoryPoint()
p1.positions = [0.0, 0.0, 0.0, 0.0]
p1.velocities = [0.0, 0.0, 0.0, 0.0]
p1.accelerations = [0.0, 0.0, 0.0, 0.0]
p1.effort = []
p1.time_from_start = rospy.Duration( 0.1 )
msg.goal.trajectory.points.append( p1 )

p2 = trajectory_msgs.msg.JointTrajectoryPoint()
p2.positions = [0.25, 0.5, 0.25, -0.5]
p2.velocities =  [0.1, 0.1, 0.1, -0.1]
p2.accelerations = [0.0, 0.0, 0.0, 0.0]
p2.effort = []
p2.time_from_start = rospy.Duration( 1 )
msg.goal.trajectory.points.append( p2 )

p3 = trajectory_msgs.msg.JointTrajectoryPoint()
p3.positions = [0.5, 1.0, 0.5, -1.0]
p3.velocities =  [0.1, 0.1, 0.1, -0.1]
p3.accelerations = [0.0, 0.0, 0.0, 0.0]
p3.effort: []
p3.time_from_start = rospy.Duration( 2 )
msg.goal.trajectory.points.append( p3 )

p4 = trajectory_msgs.msg.JointTrajectoryPoint()
p4.positions = [0.2, 1.0, 0.2, -0.5]
p4.velocities =  [-0.1, 0.0, -0.1, 0.1]
p4.accelerations = [0.0, 0.0, 0.0, 0.0]
p4.effort = []
p4.time_from_start = rospy.Duration( 4 )
msg.goal.trajectory.points.append( p4 )

p5 = trajectory_msgs.msg.JointTrajectoryPoint()
p5.positions = [0.0, -0.3, 0.0, 0.3]
p5.velocities =  [0, 0, 0, 0]
p5.accelerations = [0.0, 0.0, 0.0, 0.0]
p5.effort = []
p5.time_from_start = rospy.Duration( 5 )
msg.goal.trajectory.points.append( p5 )

p6 = trajectory_msgs.msg.JointTrajectoryPoint()
p6.positions = [0.0, 0.0, 0.0, 0.0]
p6.velocities =  [0, 0, 0, 0]
p6.accelerations = [0.0, 0.0, 0.0, 0.0]
p6.effort = []
p6.time_from_start = rospy.Duration( 7 )
msg.goal.trajectory.points.append( p6 )


print( "#### 5 ####" )

pub.publish( msg )
rospy.sleep( rospy.Duration( 1.0 ))
pub.publish( msg )

print( "#### 6 ####" )

"""
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

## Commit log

2022-07-02 Initial upload. Model tested in rviz only so far.
    [diana_gripper.scad, diana_gripper.xacro, diana_gripper_base_complete_v1.stl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]
2022-07-04 Add slanted finger with ridges.
    [finray_finger.scad]
2022-07-04 Rename fingertip-mount frames; separate fingertips.
    [diana_gripper.xacro]
2022-07-04 Copy IMU and fingertip macros into this package.
    [fingertip.xacro, finray_finger_slanted_ridges.stl, imu_gy521.stl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]
2022-07-04 Add component datasheets and schematics to doc/ folder.
2022-07-06 Add nice circuit diagram for the TTLinker serial-RS485 converter.
2022-07-06 Updated launch file and rviz config to run real gripper.
2022-07-06 Add basic ROS driver node and follow-joint-trajectory action wrapper.
2022-07-06 Add Arduino firmware with SMS/SCS and HX711 drivers.
2022-07-07 Add launch file for "parallel gripper" GUI.
    [fake_parallel_gripper.xacro]
2022-07-08 add fingertip_simple
    [fingertip_simple.scad, fingertip_simple.stl]
2022-07-09 Node publishes a joint trajectory goal for testing the controller.
2022-07-09 Replace hardcoded topic names to allow remapping.
    Also removed offensive debugging output.
    [diana_gripper_fjtas.py]
2022-07-09 Renamed to avoid clash with package name.
    Much improved checks for Arduino sequence-number and timestamps.
    Also removed or disabled unneccessary debug output.
    [diana_gripper_driver.py]
2022-07-11 added convex hull for simple fingertip
    [fingertip_simple_hull.stl]
2022-07-11 add simple_fingertips to urdf
    [diana_gripper.xacro]
2022-07-11 add tcp to urdf
    [diana_gripper.xacro]
2022-07-12 ignoring unknown joint states to accomodate larger setups
2022-07-12 renamed follow joint trajectory action
2022-07-12 added more collision geometries to urdf
    [diana_gripper.xacro]
2022-07-12 increased gripper joint velocity limits
    [diana_gripper.xacro]
2022-07-12 fixed tcp link
    [diana_gripper.xacro]
2022-07-12 added verbosity level to error print
    [diana_gripper_driver.py]
2022-07-12 Prepare for force and IMU calibration with tara.
2022-07-13 move fingertips into separate file
    [diana_gripper.xacro, fingertips.xacro]
2022-07-13 use name parameter in xacro for digit gripper
    [diana_gripper.xacro]
2022-07-13 Restore fingertips after gripper/fingertip xacro split.
    [diana_gripper_standalone.xacro]
2022-07-13 Fix typos. Count dropped serial messages.
    [diana_gripper_driver.py]
2022-07-13 Demo gripper with one DIGIT sensor and one simple fingertip.
    [diana_gripper_standalone.xacro]
2022-07-15 Send incremental instead of fixed goal id.
    [publish_gripper_goal.py]
2022-07-20 Implement force and gyro calibration and tara command.
2022-07-20 Larger proximal tilt joint range for dual-use DIGIT gripper.
    [fake_parallel_gripper.xacro]
2022-07-21 remove unnecessarily writing print buffer
2022-08-10 added usb hub to base collision object
    [diana_gripper.xacro]
2022-08-11 add multitip fingertip
    [multitip.scad, multitip.stl]
2022-08-11 integrated multitip fingertip
    [fingertips.xacro, multitip.stl, multitip_hull.stl]
2022-12-19 Add missing inertial blocks.
    [diana_gripper.xacro]
2022-12-19 Add (fake) inertial blocks for Gazebo simulation.
    [fingertips.xacro]
2024-04-25 only standard fingertips in demo
    [diana_gripper_standalone.xacro]
2024-04-25 simplified multitip hull
    [multitip_hull.stl]
2025-02-21 increase default speed
    [multitip_hull.scad]
